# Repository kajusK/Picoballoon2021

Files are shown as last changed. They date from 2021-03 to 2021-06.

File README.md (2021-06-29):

Picoballoon Challenge 2021, Deadbadger probe
============================================

This probe was designed [Picoballoon Challenge](https://www.hvezdarna.cz/novinky/picoballoon-challenge-2021/)
organised by Brno Observatory and Planetarium. A goal of this competition
is to make a probe under 20 grams that would be launched on ballon to altitudes
around 5-15 km. Only requirement except weight is sending current altitude of the probe.

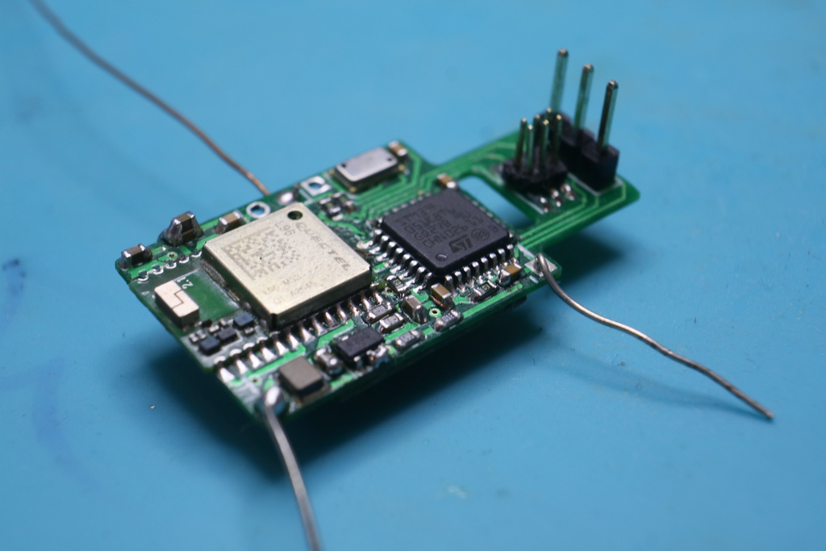
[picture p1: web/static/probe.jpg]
probe


A detailed description is available at [deadbadger.cz](https://deadbadger.cz/projects/picoballoon-2021),
tracking site is at [bal.deadbadger.cz](https://bal.deadbadger.cz).

The probe contains
  * STM32F051 MCU
  * MS5607 Pressure and temperature sensor
  * Quectel L96 GPS module with integrated antenna
  * RFM95 LoRa Transceiver
  * MCP1640 based 3.3V boost regulator

Firmware
--------
As the commonly used [LMIC](https://github.com/matthijskooijman/arduino-lmic/tree/master/src)
library is quite bulky and far from perfect, I wrote my own LoRaWan library
inspired by [TinyLoRa](https://github.com/adafruit/TinyLoRa).

The main loop does about this:
  * Power up, initialize peripherals
  * Measure system voltages, pressure
  * Wait for GPS data or timeout
  * Power off GPS
  * Send data over LoRa (ABP, unconfirmed uplink)
  * Power off RFM95 trancesiver
  * Power off for 30 minutes
  * Repeat (GPS is powered on every 4th cycle)

Hardware
--------
The board was designed for 0.6 mm thick two sided PCB to reduce weight as
much as possible. Using thicker boards (usually 1.6 mm) changes the antenna
trace impedance, but it should not be that significant.

The programming and debug uart connectors are separated from the main layout
and this piece of the PCB will be snapped off before launch to reduce weight.

**Power consumption** with 3 V power supply
  * board topped at 50 mA with GPS searching for satellites, RFM in standby and MCU running
  * 7,3 mA with GPS powered off
  * 5,3 mA with RFM95 in sleep mode and GPS off
  * 45 uA with devices powered off

**Weight**
  * 10 g - Battery
  * ~3 g - Probe PCB with programming header
  * 12,39 g - Take off weight, officially measured

Frontend
--------
Data received by [TTN](https://www.thethingsnetwork.org/) are sent over
HTTP integration to custom web server that verifies the
auth header and stores data in sqlite database.

User frontend is written in python, it shows all received packets, flight route
and current position on a [map](https://api.mapy.cz).
The tracker is available at [bal.deadbadger](https://bal.deadbadger.cz)

To run the frontend in docker, run
```
docker build -t picoballon .
mkdir /srv/probe
touch /srv/probe/database.sqlite
# set token to use in auth header
echo "someuser:somepassword" > /srv/probe/token.txt
docker run -v /srv/probe/data:/project/cloud_data --mount type=bind,source=/srv/probe/database.sqlite,target=/project/database.sqlite --mount type=bind,source=/srv/probe/credentials.txt,target=/project/credentials.txt -p 8081:80 --name picoballon -d picoballon
```

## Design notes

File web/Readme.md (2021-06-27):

### app.py
* run flask application in current context
* endpoint() authorizes incoming data, adds timestamp, make defaultdic and send data to db.py for storing into database
* provide_data() fetches all data from database and handles invalid values, return data in pretty format (rounded, with suffixes)
* functions provide_data_table(), provide_data_markers(), provide_data_graphs() prepares data for markers, summary table and graphs, which are delivered using index() to index.html, for webuser to see

### db.py
* creates database and its structure if needed
* prepare_data() extracts all usefull data from received defaultdic, zero values and strings are treated as missing, sends data to store_data() for storing into sqlite3 database
* can also fetch all data from database (fetch_all_data())

### index.html
* uses bootstrap 5 for responsive website
* api.mapy.cz displays map with markers (and their cards) and balloon route
* scrollable summary table
* section about and picture of probe
* graphs with change of temperature and altitude

### /tests
* test_app() provides various tests to determine endpoint() and class Database works correctly

### Database structure in details:
* timestamp (int)
* freq (real) - communication frequency
* rssi (int) - received signal strength indication (in dbm)
* pressure_pa (integer) - air pressure (in pascal)
* temp_c (real) & core_temp_c - outside temperature and temperature of core (in C°)
* alt_m (int) - altitude (in metres)
* lat & lon (real) - latitude and longitude from GPS
* bat_mv (int) - battery voltage (in milivolts)
* loop_time_s (int) - processor time awake (in seconds)
* lat_gw (real) & lon_gw (real) - latitude and longitude from gateway
* alt_m (int) - altitude (in metres) from gateway
* json (text) - raw received data

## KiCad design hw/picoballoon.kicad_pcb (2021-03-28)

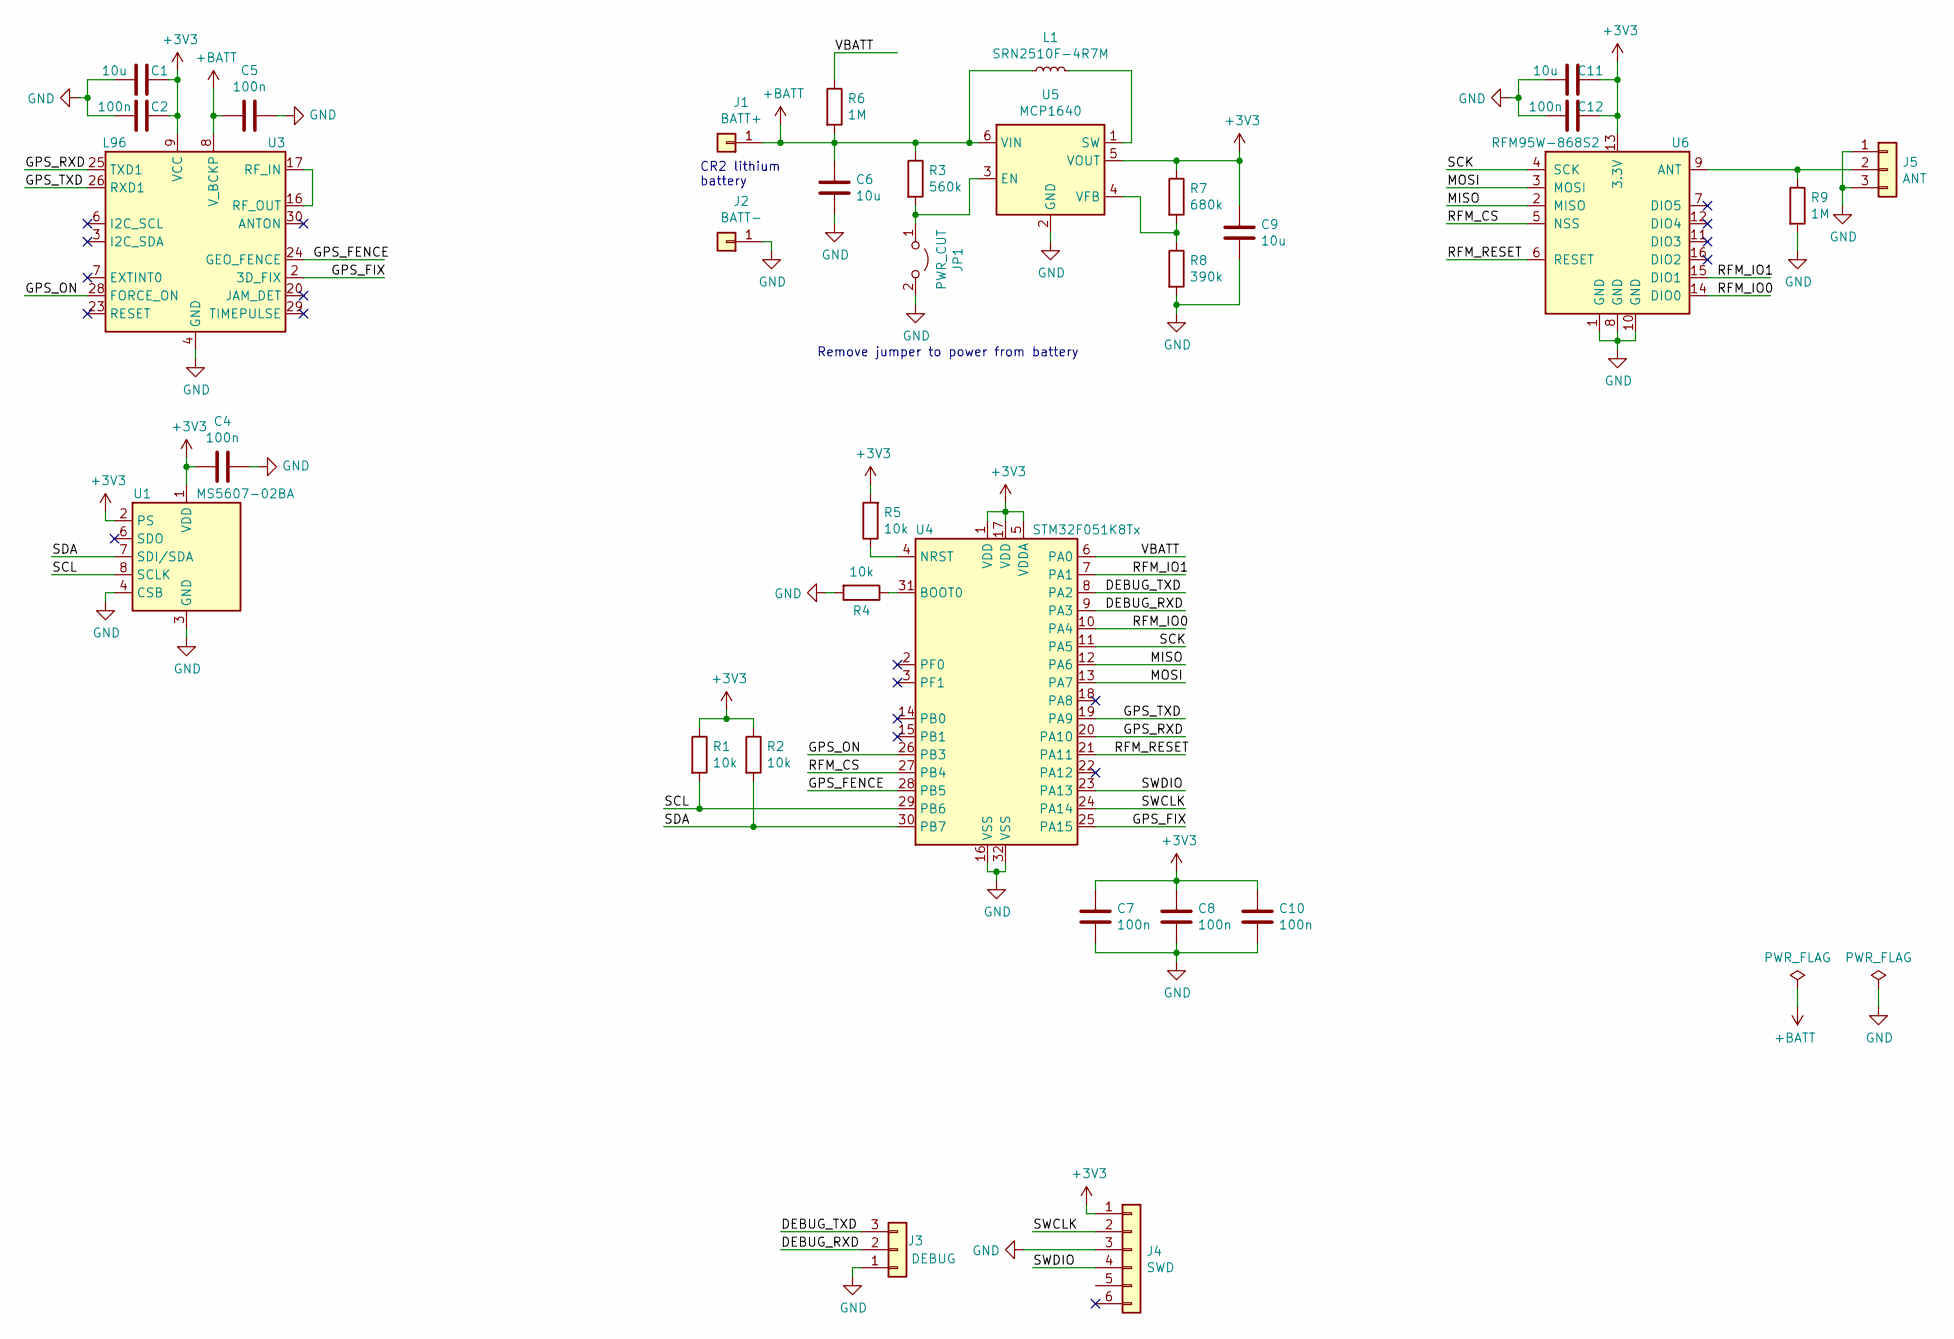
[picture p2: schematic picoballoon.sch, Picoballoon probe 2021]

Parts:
C1, C6, C9, C11: 10u; C_0603_1608Metric
C2, C4, C5, C7, C8, C10, C12: 100n; C_0603_1608Metric
J1: BATT+; PinSocket_1x01_P2.54mm_Vertical
J2: BATT-; PinHeader_1x01_P2.54mm_Vertical
J3: DEBUG; PinHeader_1x03_P2.54mm_Vertical
J4: SWD; PinHeader_2x03_P1.27mm_Vertical_SMD
J5: ANT; PinHeader_1x03_P2.54mm_Vertical
JP1: PWR_CUT; SolderJumper-2_P1.3mm_Open_Pad1.0x1.5mm
L1: SRN2510F-4R7M; L_Abracon_ASPI-3012S
R1, R2, R4, R5: 10k; R_0603_1608Metric
R3: 560k; R_0603_1608Metric
R6, R9: 1M; R_0603_1608Metric
R7: 680k; R_0603_1608Metric
R8: 390k; R_0603_1608Metric
U1: MS5607-02BA; LGA-8_3x5mm_P1.25mm
U3: L96; Quectel_L96
U4: STM32F051K8Tx; LQFP-32_7x7mm_P0.8mm
U5: MCP1640; SOT-23-6
U6: RFM95W-868S2; HOPERF_RFM9XW_SMD

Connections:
+3V3: C1.1, C2.1, C4.2, C7.1, C8.1, C9.1, C10.1, C11.1, C12.1, J4.1, R1.1, R2.1, R5.2, R7.1, U1.1 (VDD), U1.2 (PS), U3.9 (VCC), U4.1 (VDD), U4.5 (VDDA), U4.17 (VDD), U5.5 (VOUT), U6.13 (3.3V)
+BATT: C5.2, C6.1, J1.1, L1.1, R3.1, R6.2, U3.8 (V_BCKP), U3.23 (RESET), U5.6 (VIN)
/DEBUG_RXD: J3.2, U4.9 (PA3)
/DEBUG_TXD: J3.3, U4.8 (PA2)
/GPS_FENCE: U3.24 (GEO_FENCE), U4.28 (PB5)
/GPS_FIX: U3.2 (3D_FIX), U4.25 (PA15)
/GPS_ON: U3.28 (FORCE_ON), U4.26 (PB3)
/GPS_RXD: U3.25 (TXD1), U4.20 (PA10)
/GPS_TXD: U3.26 (RXD1), U4.19 (PA9)
/MISO: U4.12 (PA6), U6.2 (MISO)
/MOSI: U4.13 (PA7), U6.3 (MOSI)
/RFM_CS: U4.27 (PB4), U6.5 (NSS)
/RFM_IO0: U4.10 (PA4), U6.14 (DIO0)
/RFM_IO1: U4.7 (PA1), U6.15 (DIO1)
/RFM_RESET: U4.21 (PA11), U6.6 (RESET)
/SCK: U4.11 (PA5), U6.4 (SCK)
/SCL: R1.2, U1.8 (SCLK), U4.29 (PB6)
/SDA: R2.2, U1.7 (SDI/SDA), U4.30 (PB7)
/SWCLK: J4.2, U4.24 (PA14)
/SWDIO: J4.4, U4.23 (PA13)
/VBATT: R6.1, U4.6 (PA0)
GND: C1.2, C2.2, C4.1, C5.1, C6.2, C7.2, C8.2, C9.2, C10.2, C11.2, C12.2, J2.1, J3.1, J4.3, J5.1, J5.3, JP1.2 (B), R4.2, R8.2, R9.2, U1.3 (GND), U1.4 (CSB), U1.5 (CSB), U3.4 (GND), U3.5 (GND), U3.10 (GND), U3.11 (GND), U3.12 (GND), U3.13 (GND), U3.14 (GND), U3.15 (GND), U3.18 (GND), U3.19 (GND), U3.21 (GND), U3.22 (GND), U3.27 (GND), U3.31 (GND), U4.16 (VSS), U4.32 (VSS), U5.2 (GND), U6.1 (GND), U6.8 (GND), U6.10 (GND)
unnamed: J5.2, R9.1, U6.9 (ANT)
unnamed: JP1.1 (A), R3.2, U5.3 (EN)
unnamed: L1.2, U5.1 (SW)
unnamed: R4.1, U4.31 (BOOT0)
unnamed: R5.1, U4.4 (NRST)
unnamed: R7.2, R8.1, U5.4 (VFB)
unnamed: U3.16 (RF_OUT), U3.17 (RF_IN)

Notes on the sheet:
CR2 lithium battery
Remove jumper to power from battery

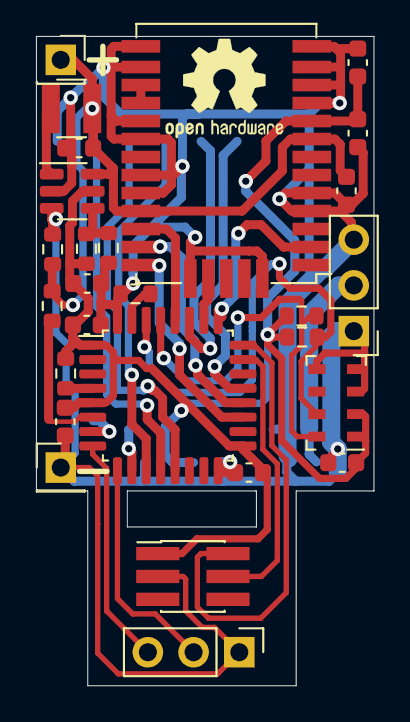
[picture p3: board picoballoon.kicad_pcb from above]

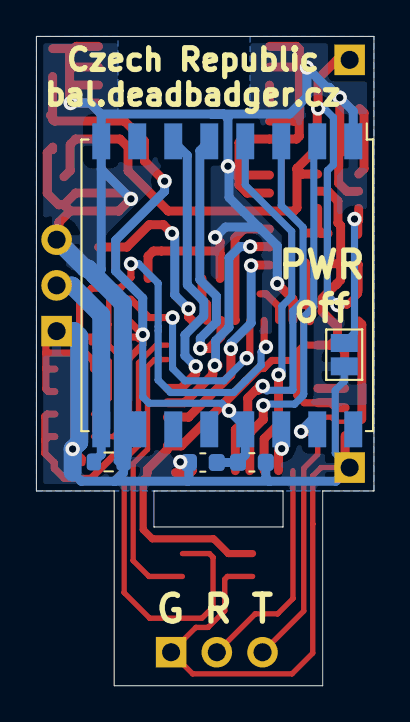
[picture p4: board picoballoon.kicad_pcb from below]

Board: 2 copper layers, 18.8 x 36.1 mm, 32 parts (5 on the bottom side), 29 nets.

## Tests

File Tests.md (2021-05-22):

# Development tests
* Send GPS to sleep, measure supply current dropped significantly, wake it up, make sure NMEA data are coming
* Send all devices to sleep/suspend, measure the current is in range of uA
* Make sure the GPS is able to get fix in the first fix scenario
* Make sure the GPS gets fix within 10 seconds if had fix before and was sleeping for 30 minutes afterwards

# Prod tests
* Connect battery, the device should initialize, measure all required data and send it over LoRa to cloud
* Make sure the current drops to uA range
* Make sure the device wakes up after 30 minutes and sends data again
* Make sure the device times out waiting for GPS if no GPS signal is available
* Put device in freezer for a week, make sure it continues to operate for the whole time

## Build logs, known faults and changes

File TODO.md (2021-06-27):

# For next board revision
* Connect MCU reset to the programming header, it's not possible to flash the MCU when it's in sleep mode
* RFU consumes around 500 uA when pins are floating in sleep mode - tie Reset and all SPI pins to vcc with a resistor - interestingly, the power consumption rises from 100 uA to 500 uA slowly when no resistors are used
* Issue between schematic and PCB - L96 reset pin is connected to BATT+ on PCB, but not in schematic, should be floating or tied to vcc
* connect all unused MCU pins to ground to reduce power consumption due to noise
* put 0R resistors in power line of each device for measuring the power consumption of each piece
* Remove GPS fencing pin and connect EXTINT0 pin for entering GPS standby immediately after powering up the MCU.
* add pull down to FORCE_ON GPS pin
* Test if L96 works, was not able to get first fix below 20min on the prototype

# Next software revision
* Consider sending AGPS data over lora to device to speed up the GPS fix

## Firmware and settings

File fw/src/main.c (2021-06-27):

/*
 * Copyright (C) 2021 Jakub Kaderka
 *
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
 * You should have received a copy of the GNU General Public License
 * along with this program.  If not, see <https://www.gnu.org/licenses/>.
 */

/**
 * @file    app/main.c
 * @brief   Main file for deadbadger.cz picoballoon
 *
 * @addtogroup app
 *
 * @{
 */

#include <types.h>

#include <libopencm3/stm32/rcc.h>
#include <libopencm3/stm32/i2c.h>
#include <libopencm3/stm32/spi.h>

#include <hal/io.h>
#include <hal/adc.h>
#include <hal/i2c.h>
#include <hal/spi.h>
#include <hal/uart.h>
#include <hal/rtc.h>
#include <hal/exti.h>
#include <hal/power.h>
#include <hal/flash.h>
#include <utils/time.h>

#include <modules/log.h>
#include <modules/lora.h>
#include <drivers/gps.h>
#include <drivers/ms5607.h>
#include <drivers/si7020.h>
#include <drivers/rfm.h>

#include "config.h"

/** LoRa packet payload format */
typedef struct {
    uint32_t press_Pa;      /** Air pressure in deca Pascals (*10) */
    int16_t temp_dc;        /** Temperature in deci Celsius (/10) */
    int8_t core_temp_c;     /** MCU core temperature in degrees Celsius */
    uint16_t bat_mv;        /**< Voltage of the battery/supercap */
    uint16_t gps_alt_m;     /** GPS Altitude in meters */
    float lat;              /** Latitude in decimal degrees */
    float lon;              /** Longitude in decimal degrees */
    uint8_t loop_time_s;    /**< Time since wake up until packet creation */
} __attribute__((packed)) telemetry_packet_t;

/** Persistent data stored in the flash memory between consecutive runs */
typedef struct {
    uint32_t counter;       /**< LoRa Packet counter */
    rfm_lora_region_t region;   /**< RFM LoRa region used recently */
} persist_data_t;

/** Memory locations for persistent data defined in linker file */
extern const persist_data_t persist1;
extern const persist_data_t persist2;

static gps_desc_t gps_desc;
static ms5607_desc_t ms5607_desc;
static rfm_desc_t rfm_desc;

/** The Thing Network auth data */
static const uint8_t lora_dev_addr[4] = TTN_DEV_ADDR;
static const uint8_t lora_nwks_key[16] = TTN_NWKSKEY;
static const uint8_t lora_apps_key[16] = TTN_APPSKEY;

/**
 * Get LoRa region based on recent known location
 *
 * @param gps_lat   Latitude
 * @param gps_lon   Longitude
 * @return Selected LoRa region
 */
static rfm_lora_region_t App_GetRegion(nmea_float_t gps_lat,
        nmea_float_t gps_lon)
{
    rfm_lora_region_t region = RFM_REGION_EU863;
    int16_t lat = gps_lat.num / gps_lat.scale;
    int16_t lon = gps_lon.num / gps_lon.scale;

    if (lon > -180 && lon < -50) {
        region = RFM_REGION_US902;
        Log_Info("GPS", "Using US LoRa region");
    /* Australia, New Zealand */
    } else if  (lat > -50 && lat < -7 && lon > 100 && lon < 170) {
        region = RFM_REGION_AU915;
        Log_Info("GPS", "Using AU LoRa region");
    /* Japan, Malaysia, etc. */
    } else if (lon > 87 && lon < 180 && lat < 50) {
        region = RFM_REGION_AS920;
        Log_Info("GPS", "Using AS LoRa region");
    } else {
        Log_Info("GPS", "Using EU LoRa region");
    }

    return region;
}

/**
 * Save persistent data to flash memory
 *
 * @param counter   LoRa tx counter value
 * @param region    RFM LoRaWan region recently used
 */
static void App_SavePersistentData(uint32_t counter, rfm_lora_region_t region)
{
    persist_data_t data;
    uint32_t addr = (uint32_t)&persist1;

    if (persist1.counter == (uint32_t)-1) {
        addr = (uint32_t)&persist1;
    } else if (persist2.counter == (uint32_t)-1) {
        addr = (uint32_t)&persist2;
    } else if (persist1.counter > persist2.counter) {
        addr = (uint32_t)&persist2;
    } else {
        addr = (uint32_t)&persist1;
    }
    data.counter = counter;
    data.region = region;

    Flashd_WriteEnable();
    Flashd_ErasePage(addr);
    Flashd_Write(addr, (uint8_t *)&data, sizeof(data));
    Flashd_WriteDisable();
}

/**
 * Load saved persistent data
 *
 * @param [out] counter     Recently used LoRa TX counter value
 * @param [out] region      Recently used LoRa region
 */
static void App_LoadPersistentData(uint32_t *counter, rfm_lora_region_t *region)
{
    const persist_data_t *data;

    if (persist1.counter == (uint32_t)-1 && persist2.counter == (uint32_t)-1) {
        if (counter != NULL) {
            *counter = 0;
        }
        if (region != NULL) {
            *region = RFM_REGION_EU863;
        }
        return;
    } else if (persist1.counter == (uint32_t)-1) {
        data = &persist2;
    } else if (persist2.counter == (uint32_t)-1) {
        data = &persist1;
    } else if (persist1.counter > persist2.counter) {
        data = &persist1;
    } else {
        data = &persist2;
    }

    if (counter != NULL) {
        *counter = data->counter;
    }
    if (region != NULL) {
        *region = data->region;
    }
}

static void App_GpsOn(void)
{
    IOd_SetLine(LINE_GPS_ON, 1);
}

static void App_GpsOff(void)
{
    IOd_SetLine(LINE_GPS_ON, 0);
    Gps_Backup(&gps_desc);
}

/**
 * Wait for valid GPS data or timeout
 * @param timeout_s     Timeout in seconds for waiting for fix
 * @return True if have valid data, false if timed out
 */
static bool App_WaitGps(uint32_t timeout_s)
{
    uint32_t start_ts;

    Log_Info("App", "Waiting for GPS");

    EXTId_EnableEvent(PAD_GPS_FIX);
    if (IOd_GetLine(LINE_GPS_FIX) != 1) {
        /* Go to sleep until GPS fix is obtained or timeout */
        RTCd_SetAlarmInSeconds(timeout_s, NULL);
        Powerd_Stop();
    }
    EXTId_Disable(PAD_GPS_FIX);

    if (IOd_GetLine(LINE_GPS_FIX) == 0) {
        return false;
    }
    /* Wait for 1,5 second to get the whole NMEA data */
    start_ts = millis();
    while (Gps_Loop(&gps_desc) == NULL && (millis() - start_ts) < 1500) {
        ;
    }

    return Gps_Get(&gps_desc) != NULL;
}

/**
 * Get the time difference between start time and current time from RTC
 *
 * @return time in seconds
 */
static uint32_t time_elapsed_s(struct tm *tm_start)
{
    struct tm tm_now;
    time_t start;
    time_t now;

    RTCd_GetTime(&tm_now);
    start = mktime(tm_start);
    now = mktime(&tm_now);

    return (uint32_t)difftime(now, start);
}

static void App_Loop(void)
{
    telemetry_packet_t packet = {0};
    const gps_info_t *gps;
    int32_t temp_mdeg = 0;
    uint32_t press_Pa = 0;
    struct tm tm;
    uint32_t tx_counter = 0;
    rfm_lora_region_t region = RFM_REGION_EU863;
    bool use_gps = false;
    uint32_t gps_timeout_s = GPS_FIX_TIMEOUT_S;

    RTCd_GetTime(&tm);
    App_LoadPersistentData(&tx_counter, &region);
    if (tx_counter % TELEMETRY_GPS_SKIP == 0) {
        if (tx_counter % (TELEMETRY_GPS_SKIP*TELEMETRY_GPS_FULL_SKIP) == 0) {
            gps_timeout_s = GPS_FULL_TIMEOUT_S;
        }
        Log_Info("App", "Using GPS, timeout %d seconds", gps_timeout_s);
        App_GpsOn();
        use_gps = true;
    }

    Adcd_UpdateVdda();
    packet.bat_mv = Adcd_ReadMv(CHN_VBATT);
    packet.core_temp_c = Adcd_ReadTempDegC();
    Adcd_Sleep();

    if (!MS5607_Read(&ms5607_desc, MS5607_OSR1024, &press_Pa, &temp_mdeg)) {
        packet.press_Pa = 0;
        packet.temp_dc = 0;
    } else {
        packet.press_Pa = press_Pa;
        packet.temp_dc = temp_mdeg / 100;
    }

    /* wait for fix */
    if (use_gps && !App_WaitGps(gps_timeout_s)) {
        Log_Info("App", "Failed to get GPS position");
    }
    gps = Gps_Get(&gps_desc);
    App_GpsOff();

    if (gps != NULL) {
        Log_Info("App", "Got GPS");
        region = App_GetRegion(gps->lat, gps->lon);
        packet.gps_alt_m = gps->altitude_dm/10;
        packet.lat = ((float) gps->lat.num) / gps->lat.scale;
        packet.lon = ((float) gps->lon.num) / gps->lon.scale;
    } else {
        if (use_gps) {
            /* Failed to obtain GPS fix, get default region */
            region = RFM_REGION_EU863;
        }
        packet.gps_alt_m = 0;
        packet.lat = 0;
        packet.lon = 0;
    }

    packet.loop_time_s = time_elapsed_s(&tm);

    Log_Info(NULL, "TX counter %d", tx_counter);
    Log_Info(NULL, "Pressure %d Pa", packet.press_Pa);
    Log_Info(NULL, "Temperature %d C", packet.temp_dc/10);
    Log_Info(NULL, "Core temp %d C", packet.core_temp_c);
    Log_Info(NULL, "Battery voltage %d mV", packet.bat_mv);
    Log_Info(NULL, "Latitude %f", packet.lat);
    Log_Info(NULL, "Longitude %f", packet.lon);
    Log_Info(NULL, "GPS alt %d m", packet.gps_alt_m);
    Log_Info(NULL, "Loop time %d s", packet.loop_time_s);
    Log_Info(NULL, "Sending data");

    /* RFM module initialization postponed here to save power */
    RFM_LoraInit(&rfm_desc);
    RFM_SetLoraParams(&rfm_desc, RFM_BW_125k, RFM_SF_10);
    RFM_SetPowerDBm(&rfm_desc, 17);
    RFM_SetLoraRegion(&rfm_desc, region);

    /* Save LoRa tx counter + 1 (in case, power dies before saving) */
    Lora_SetCounters(0, tx_counter);
    App_SavePersistentData(tx_counter+1, region);

    if (!Lora_Send((uint8_t *) &packet, sizeof(packet))) {
        Log_Error(NULL, "Failed to send data over LoRaWan!");
    }
    Log_Info(NULL, "Powering off");
    RFM_PowerOff(&rfm_desc);
}

static void lora_send_cb(const uint8_t *data, size_t len)
{
    RFM_LoraSend(&rfm_desc, data, len);
}

int main(void)
{
    /* Initialize clock system, IO pins and systick */
    IOd_Init();
    Time_Init();

    /* early init - debug output */
    UARTd_Init(USART_DEBUG_TX, 115200);
    Log_Init(USART_DEBUG_TX);
    Log_Info(NULL, "PicoBalloon Challenge 2021");
    Log_Info(NULL, "Launched from Brno Observatory, Czech Republic");
    Log_Info(NULL, "bal.eadbadger.cz");

    I2Cd_Init(1, false);
    SPId_Init(1, SPID_PRESC_2, SPI_MODE_0);
    RTCd_Init(false);
    Adcd_Init();

    UARTd_Init(USART_GPS_TXD, 9600);
    Gps_Init(&gps_desc, USART_GPS_TXD);

    if (!MS5607_Init(&ms5607_desc, 1, MS5607_ADDR_1)) {
        Log_Error(NULL, "MS5607 pressure sensor not responding");
    }

    if (!RFM_Init(&rfm_desc, 1, LINE_RFM_CS, LINE_RFM_RESET, LINE_RFM_IO0)) {
        Log_Error(NULL, "RFM module not responding!");
        delay_ms(1000);
        /* RFM module is crucial, it makes no sense to continue without it */
        Powerd_Reboot();
    }
    Lora_InitAbp(lora_send_cb);
    Lora_SetAbpKeys(lora_dev_addr, lora_nwks_key, lora_apps_key);

    EXTId_SetMux(LINE_GPS_FIX);
    EXTId_SetEdge(PAD_GPS_FIX, EXTID_RISING);

    Log_Info(NULL, "System initialized, running main loop");
    Log_SetLevel(LOG_ERROR);

    /* ================ TODO ================ */
    /* debugging purposes only, remove for production */
    Log_SetLevel(LOG_DEBUG);
    delay_ms(5000);
    /* ================ TODO ================ */

    while (1) {
        /* set alarm first to ensure precise periods */
        RTCd_SetAlarmInSeconds(TELEMETRY_PERIOD_MIN*60, NULL);
        App_Loop();

        Adcd_Sleep();
        App_GpsOff();
        RFM_PowerOff(&rfm_desc);
        Powerd_Off();
        Log_Error(NULL, "Failed to power off the MCU!");
        delay_ms(1000);
        Powerd_Reboot();
    }
}

/** @} */

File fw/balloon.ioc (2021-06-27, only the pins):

Mcu.UserName=STM32F051K8Tx
PA0.GPIO_Label=VBATT
PA0.Signal=ADC_IN0
PA1.GPIO_Label=RFM_IO1
PA1.Signal=GPIO_Input
PA10.GPIO_Label=GPS_RXD
PA10.Signal=USART1_RX
PA11.GPIO_Label=RFM_RESET
PA11.Signal=GPIO_Output
PA12.Signal=GPIO_Analog
PA13.Signal=SYS_SWDIO
PA14.Signal=SYS_SWCLK
PA15.GPIO_Label=GPS_FIX
PA15.Signal=GPIO_Input
PA2.GPIO_Label=DEBUG_TX
PA2.Signal=USART2_TX
PA3.GPIO_Label=DEBUG_RX
PA3.Signal=USART2_RX
PA4.GPIO_Label=RFM_IO0
PA4.Signal=GPIO_Input
PA5.Signal=SPI1_SCK
PA6.Signal=SPI1_MISO
PA7.Signal=SPI1_MOSI
PA8.Signal=GPIO_Analog
PA9.GPIO_Label=GPS_TXD
PA9.Signal=USART1_TX
PB0.Signal=GPIO_Analog
PB1.Signal=GPIO_Analog
PB3.GPIO_Label=GPS_ON
PB3.Signal=GPIO_Output
PB4.GPIO_Label=RFM_CS
PB4.Signal=GPIO_Output
PB5.GPIO_Label=GPS_FENCE
PB5.Signal=GPIO_Input
PB6.Signal=I2C1_SCL
PB7.Signal=I2C1_SDA
PF0-OSC_IN.Signal=GPIO_Analog
PF1-OSC_OUT.Signal=GPIO_Analog

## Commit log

2021-03-28 Added pcb design
    [picoballoon-B_Cu.gbr, picoballoon-B_Mask.gbr, picoballoon-B_Paste.gbr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]
2021-05-22 Rewrote the GPS timeouts and lora regions switching
2021-05-25 Fixed ADC readings and sleep modes
    [main.c]
2021-06-26 function endpoint, class Database in separate file db.py, create Readme
    Function database_status() checks if database.sqlite exists, if not, create one.
    Function endpoint() used for inserting data into database.
    Readme.db contains explanation of database structure.
2021-06-26 incorporate bootstrap
    page is separated into 2 columns,
    the map has responsive size, is centered and zoomed to capture all markers, sizes of markers' cards are fixed
    sizes of the summary table and the image of probe are responsive
2021-06-26 calculate altitude from pressure
2021-06-26 picture of probe
2021-06-27 Added notes for future board revisions
2021-06-27 Reducing power consumption, updated region switching logic
2021-06-27 Changed default pin states to (hopefully) reduce power consumption
2021-06-27 Updated probe image and webpage description
2021-06-27 fix temperature handling, fix tests authorization
2021-06-27 Send pressure in Pa

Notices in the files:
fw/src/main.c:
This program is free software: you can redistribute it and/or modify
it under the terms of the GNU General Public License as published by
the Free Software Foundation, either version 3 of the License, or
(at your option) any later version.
